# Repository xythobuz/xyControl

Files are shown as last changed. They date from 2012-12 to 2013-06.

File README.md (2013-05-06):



[xyControl][gh] is a Quadrocopter Flight Controller based on Atmels Atmega2560 microcontroller.
It features 512KB SRAM on-board, using the external memory interface of this processor.
Also included is a switched power supply as well as a USB connection to communicate with and program the target.
All I/O pins, including 3 additional UARTs, SPI, I2C (TWI) and 16 ADC Channels, are accessible via standard 2.54mm connectors.
The Board can be powered from an external stable 5V supply, USB or 7V or more, via the on-board switched power supply. All voltage sources can be selected via jumpers.

[][xy1]
[][xy2]
[][ss]

## Flight Control Software Flow

Three tasks are controlling the Quadrocopter Orientation in Space.

+ The [Orientation Task][orient] reads the Gyroscope and Accelerometer and calculates the current Roll and Pitch angles. They are stored in the global struct "orientation".
+ The [PID Task][pid] is then feeding these angles into two PID controllers. Their output is then used by...
+ The [Set Task][set], which calculates the motor speeds and gives them to...
+ The [motor task][motor], which sends the new values via TWI to the motor controllers.

# Supported Hardware

+ Gyroscope L3GD20, code based on the [Adafruit Example][adafruit].
+ Accelerometer and Magnetometer LSM303DLHC, code based on the [Pololu Example][pololucode].
+ I got both of these Sensors on the [MinIMU-9 v2][pololu].
+ Brushless Motor Driver [BL-Ctrl V1.2][ctrl] with eg. the [Robbe Roxxy Outrunner 2824-34][mot] Brushless Motor.
+ BTM-222 Bluetooth UART Bridge ([PCB][bt])

## External Memory ([xmem.h][xmem])

The external memory consists of a 512Kx8 SRAM, bank-switched onto the 16bit avr address space.
This gives us 8 memory banks, consisting of 56KB. All memory from 0x0000 to 0x21FF is the AVRs internal memory. The memory banks are switched into 0x2200 to 0xFFFF.
This gives us 8 banks with 56KB each, resulting in 448KB external RAM.

The data and bss memory sections, as well as the Stack are located in the internal RAM. The external RAM is used only for dynamically allocated memory.

## Orientation Calculation ([orientation.h][orient])

Calculates the current angles of the platform, using Gyroscope and Accelerometer Data with a Kalman Filter. It is using this slightly modified [Kalman Filter Implementation][kalman] by Linus Helgesson.

# PC and Android Tools

You can find some PC Software in the [tools][tools] directory. Each one should be accompanied by it's own Readme file.

## UART-Flight Status Packet Format

    printf("t%.2f %.2f %.2f\n", kp, ki, kd);
    printf("u%.2f %.2f\n", pid_output[1], pid_output[0]); // Pitch, Roll
    printf("v%i %i %i %i\n", motorSpeed[0], ..., motorSpeed[3]);
    printf("w%.2f\n", orientation.pitch);
    printf("x%.2f\n", orientation.roll);
    printf("y%.2f\n", orientation.yaw);
    printf("z%.2f\n", getVoltage());

# Software used

 + [Peter Fleurys TWI Library][fleury]

# License

Peter Fleurys TWI Library (twi.c & twi.h) is released under the [GNU GPL license][gpl].

Everything else is released under a BSD-Style license. See the [accompanying COPYING file][bsd].

 [sss]: http://www.xythobuz.de/img/xyCopterOsci_small.png
 [ss]: http://www.xythobuz.de/img/xyCopterOsci.png
 [xy1s]: http://www.xythobuz.de/img/xycontrol1_small.jpg
 [xy1]: http://www.xythobuz.de/img/xycontrol1.jpg
 [xy2s]: http://www.xythobuz.de/img/xycontrol2_small.jpg
 [xy2]: http://www.xythobuz.de/img/xycontrol2.jpg
 [gh]: http://www.xythobuz.de/xycontrol/
 [logo]: http://www.xythobuz.de/xycontrol/logo.png
 [adafruit]: https://github.com/adafruit/Adafruit_L3GD20
 [pololucode]: https://github.com/pololu/LSM303
 [pololu]: http://www.pololu.com/catalog/product/1268
 [ctrl]: http://www.mikrokopter.de/ucwiki/en/BL-Ctrl_V1.2
 [mot]: http://www.conrad.de/ce/de/product/231867
 [bt]: http://xythobuz.de/bluetooth.html
 [kalman]: http://www.linushelgesson.se/2012/04/pitch-and-roll-estimating-kalman-filter-for-stabilizing-quadrocopters/
 [fleury]: http://homepage.hispeed.ch/peterfleury/avr-software.html
 [gpl]: http://www.gnu.org/licenses/gpl.html
 [bsd]: https://github.com/xythobuz/xyControl/blob/master/COPYING
 [xmem]: https://github.com/xythobuz/xyControl/blob/master/include/xmem.h
 [orient]: https://github.com/xythobuz/xyControl/blob/master/include/orientation.h
 [tools]: https://github.com/xythobuz/xyControl/tree/master/tools
 [pid]: https://github.com/xythobuz/xyControl/blob/master/include/pid.h
 [set]: https://github.com/xythobuz/xyControl/blob/master/include/set.h
 [motor]: https://github.com/xythobuz/xyControl/blob/master/include/motor.h

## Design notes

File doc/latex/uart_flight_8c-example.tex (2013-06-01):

\hypertarget{uart_flight_8c-example}{\section{uart\-Flight.\-c}
}

\begin{DoxyCodeInclude}
\textcolor{comment}{/*}
\textcolor{comment}{ * uartFlight.c}
\textcolor{comment}{ *}
\textcolor{comment}{ * Copyright (c) 2013, Thomas Buck <xythobuz@me.com>}
\textcolor{comment}{ * All rights reserved.}
\textcolor{comment}{ *}
\textcolor{comment}{ * Redistribution and use in source and binary forms, with or without}
\textcolor{comment}{ * modification, are permitted provided that the following conditions}
\textcolor{comment}{ * are met:}
\textcolor{comment}{ *}
\textcolor{comment}{ * - Redistributions of source code must retain the above copyright notice,}
\textcolor{comment}{ *   this list of conditions and the following disclaimer.}
\textcolor{comment}{ *}
\textcolor{comment}{ * - Redistributions in binary form must reproduce the above copyright}
\textcolor{comment}{ *   notice, this list of conditions and the following disclaimer in the}
\textcolor{comment}{ *   documentation and/or other materials provided with the distribution.}
\textcolor{comment}{ *}
\textcolor{comment}{ * THIS SOFTWARE IS PROVIDED BY THE COPYRIGHT HOLDERS AND CONTRIBUTORS}
\textcolor{comment}{ * "AS IS" AND ANY EXPRESS OR IMPLIED WARRANTIES, INCLUDING, BUT NOT LIMITED}
\textcolor{comment}{ * TO, THE IMPLIED WARRANTIES OF MERCHANTABILITY AND FITNESS FOR A PARTICULAR}
\textcolor{comment}{ * PURPOSE ARE DISCLAIMED. IN NO EVENT SHALL THE COPYRIGHT HOLDER OR}
\textcolor{comment}{ * CONTRIBUTORS BE LIABLE FOR ANY DIRECT, INDIRECT, INCIDENTAL, SPECIAL,}
\textcolor{comment}{ * EXEMPLARY, OR CONSEQUENTIAL DAMAGES (INCLUDING, BUT NOT LIMITED TO,}
\textcolor{comment}{ * PROCUREMENT OF SUBSTITUTE GOODS OR SERVICES; LOSS OF USE, DATA, OR}
\textcolor{comment}{ * PROFITS; OR BUSINESS INTERRUPTION) HOWEVER CAUSED AND ON ANY THEORY OF}
\textcolor{comment}{ * LIABILITY, WHETHER IN CONTRACT, STRICT LIABILITY, OR TORT (INCLUDING}
\textcolor{comment}{ * NEGLIGENCE OR OTHERWISE) ARISING IN ANY WAY OUT OF THE USE OF THIS}
\textcolor{comment}{ * SOFTWARE, EVEN IF ADVISED OF THE POSSIBILITY OF SUCH DAMAGE.}
\textcolor{comment}{ */}
\textcolor{preprocessor}{#include <stdint.h>}
\textcolor{preprocessor}{#include <stdlib.h>}
\textcolor{preprocessor}{#include <stdio.h>}
\textcolor{preprocessor}{#include <avr/io.h>}
\textcolor{preprocessor}{#include <avr/pgmspace.h>}

\textcolor{preprocessor}{#define DEBUG 1}
\textcolor{preprocessor}{}
\textcolor{preprocessor}{#include <\hyperlink{debug_8h}{debug.h}>}
\textcolor{preprocessor}{#include <\hyperlink{tasks_8h}{tasks.h}>}
\textcolor{preprocessor}{#include <\hyperlink{error_8h}{error.h}>}
\textcolor{preprocessor}{#include <\hyperlink{xycontrol_8h}{xycontrol.h}>}
\textcolor{preprocessor}{#include <\hyperlink{time_8h}{time.h}>}
\textcolor{preprocessor}{#include <\hyperlink{uart_menu_8h}{uartMenu.h}>}
\textcolor{preprocessor}{#include <\hyperlink{serial_8h}{serial.h}>}
\textcolor{preprocessor}{#include <\hyperlink{acc_8h}{acc.h}>}
\textcolor{preprocessor}{#include <\hyperlink{gyro_8h}{gyro.h}>}
\textcolor{preprocessor}{#include <\hyperlink{mag_8h}{mag.h}>}
\textcolor{preprocessor}{#include <\hyperlink{motor_8h}{motor.h}>}
\textcolor{preprocessor}{#include <\hyperlink{orientation_8h}{orientation.h}>}
\textcolor{preprocessor}{#include <\hyperlink{pid_8h}{pid.h}>}
\textcolor{preprocessor}{#include <\hyperlink{set_8h}{set.h}>}

\textcolor{preprocessor}{#define MAXANGLE 45}
\textcolor{preprocessor}{}\textcolor{preprocessor}{#define ANGLESTEP 10}
\textcolor{preprocessor}{}\textcolor{preprocessor}{#define MAXMOTOR 255}
\textcolor{preprocessor}{}\textcolor{preprocessor}{#define MOTORSTEP 10}
\textcolor{preprocessor}{}\textcolor{preprocessor}{#define QUADFREQ 100}
\textcolor{preprocessor}{}\textcolor{preprocessor}{#define STATUSFREQ 10}
\textcolor{preprocessor}{}
\textcolor{preprocessor}{#define QUADDELAY (1000 / QUADFREQ)}
\textcolor{preprocessor}{}\textcolor{preprocessor}{#define STATUSDELAY (1000 / STATUSFREQ)}
\textcolor{preprocessor}{}
\textcolor{keywordtype}{void} flightTask(\textcolor{keywordtype}{void});
\textcolor{keywordtype}{void} statusTask(\textcolor{keywordtype}{void});
\textcolor{keywordtype}{void} controlToggle(\textcolor{keywordtype}{void});
\textcolor{keywordtype}{void} motorToggle(\textcolor{keywordtype}{void});
\textcolor{keywordtype}{void} motorUp(\textcolor{keywordtype}{void});
\textcolor{keywordtype}{void} motorDown(\textcolor{keywordtype}{void});
\textcolor{keywordtype}{void} motorForward(\textcolor{keywordtype}{void});
\textcolor{keywordtype}{void} motorBackward(\textcolor{keywordtype}{void});
\textcolor{keywordtype}{void} motorLeft(\textcolor{keywordtype}{void});
\textcolor{keywordtype}{void} motorRight(\textcolor{keywordtype}{void});
\textcolor{keywordtype}{void} parameterChange(\textcolor{keywordtype}{void});
\textcolor{keywordtype}{void} silent(\textcolor{keywordtype}{void});
\textcolor{keywordtype}{void} printRaw(\textcolor{keywordtype}{void});

\textcolor{keywordtype}{char} PROGMEM motorToggleString[] = \textcolor{stringliteral}{"Motor On/Off"};
\textcolor{keywordtype}{char} PROGMEM motorUpString[] = \textcolor{stringliteral}{"Up"};
\textcolor{keywordtype}{char} PROGMEM motorDownString[] = \textcolor{stringliteral}{"Down"};
\textcolor{keywordtype}{char} PROGMEM motorLeftString[] = \textcolor{stringliteral}{"Left"};
\textcolor{keywordtype}{char} PROGMEM motorRightString[] = \textcolor{stringliteral}{"Right"};
\textcolor{keywordtype}{char} PROGMEM motorForwardString[] = \textcolor{stringliteral}{"Forwards"};
\textcolor{keywordtype}{char} PROGMEM motorBackwardString[] = \textcolor{stringliteral}{"Backwards"};
\textcolor{keywordtype}{char} PROGMEM controlToggleString[] = \textcolor{stringliteral}{"Toggle PID"};
\textcolor{keywordtype}{char} PROGMEM parameterChangeString[] = \textcolor{stringliteral}{"Change PID Params"};
\textcolor{keywordtype}{char} PROGMEM zeroString[] = \textcolor{stringliteral}{"Angles to Zero"};
\textcolor{keywordtype}{char} PROGMEM silentString[] = \textcolor{stringliteral}{"Toggle Status Output"};
\textcolor{keywordtype}{char} PROGMEM sensorString[] = \textcolor{stringliteral}{"Raw Sensor Data"};

\textcolor{preprocessor}{#define STATE\_MOTOR (1 << 0) // 1 -> Motor On}
\textcolor{preprocessor}{}\textcolor{preprocessor}{#define STATE\_PID (1 << 1) // 1 -> PID enabled}
\textcolor{preprocessor}{}\textcolor{preprocessor}{#define STATE\_OUTPUT (1 << 2) // 1 -> No Status Output}
\textcolor{preprocessor}{}uint8\_t state = 0;

uint8\_t speed = 10;
int16\_t targetRoll = 0;
int16\_t targetPitch = 0;

uint32\_t sumFlightTask = 0, countFlightTask = 0;

\textcolor{keywordtype}{int} main(\textcolor{keywordtype}{void}) \{
    \hyperlink{group__xycontrol_ga2b3fb0734a2675e6dbdcb2c7665a708f}{xyInit}();
    \hyperlink{group__pid_ga54768e126d9accbdd7232d9fa5adfdfd}{pidInit}();
    \hyperlink{group__motor_gaa29e2982047be0f7afbb10c8d6f3f5c3}{motorInit}();
    \hyperlink{group__orientation_gaa5724492d0f54b41a8984cdde51d59df}{orientationInit}();

    \hyperlink{group__debug_gada1787bea8c10cd89775d6918f6fd324}{debugPrint}(\textcolor{stringliteral}{"Initialized Hardware"});

    \hyperlink{group__task_ga9a6ba4cb66e2fb7e3be42fb5b87fec6f}{addTask}(&flightTask);
    \hyperlink{group__task_ga9a6ba4cb66e2fb7e3be42fb5b87fec6f}{addTask}(&statusTask);

    \hyperlink{group__uartmenu_gaba6c962adeaaeca40be02fb1098312ed}{addMenuCommand}(\textcolor{charliteral}{'m'}, motorToggleString, &motorToggle);
    \hyperlink{group__uartmenu_gaba6c962adeaaeca40be02fb1098312ed}{addMenuCommand}(\textcolor{charliteral}{'w'}, motorForwardString, &motorForward);
    \hyperlink{group__uartmenu_gaba6c962adeaaeca40be02fb1098312ed}{addMenuCommand}(\textcolor{charliteral}{'a'}, motorLeftString, &motorLeft);
    \hyperlink{group__uartmenu_gaba6c962adeaaeca40be02fb1098312ed}{addMenuCommand}(\textcolor{charliteral}{'s'}, motorBackwardString, &motorBackward);
    \hyperlink{group__uartmenu_gaba6c962adeaaeca40be02fb1098312ed}{addMenuCommand}(\textcolor{charliteral}{'d'}, motorRightString, &motorRight);
    \hyperlink{group__uartmenu_gaba6c962adeaaeca40be02fb1098312ed}{addMenuCommand}(\textcolor{charliteral}{'x'}, motorUpString, &motorUp);
    \hyperlink{group__uartmenu_gaba6c962adeaaeca40be02fb1098312ed}{addMenuCommand}(\textcolor{charliteral}{'y'}, motorDownString, &motorDown);
    \hyperlink{group__uartmenu_gaba6c962adeaaeca40be02fb1098312ed}{addMenuCommand}(\textcolor{charliteral}{'p'}, controlToggleString, &controlToggle);
    \hyperlink{group__uartmenu_gaba6c962adeaaeca40be02fb1098312ed}{addMenuCommand}(\textcolor{charliteral}{'n'}, parameterChangeString, &parameterChange);
    \hyperlink{group__uartmenu_gaba6c962adeaaeca40be02fb1098312ed}{addMenuCommand}(\textcolor{charliteral}{'z'}, zeroString, &\hyperlink{group__orientation_ga0fab95dd407145abad293f7c91460eee}{zeroOrientation});
    \hyperlink{group__uartmenu_gaba6c962adeaaeca40be02fb1098312ed}{addMenuCommand}(\textcolor{charliteral}{'o'}, silentString, &silent);
    \hyperlink{group__uartmenu_gaba6c962adeaaeca40be02fb1098312ed}{addMenuCommand}(\textcolor{charliteral}{'r'}, sensorString, &printRaw);

    \hyperlink{group__xycontrol_ga783aead7f97dd462a9af56b7fc3b228f}{xyLed}(\hyperlink{group__xycontrol_ggaadcb6002d2b42fdfe01490f730ab00a6ad80f13022b6d309268fadc7b1da89cb9}{LED\_RED}, \hyperlink{group__xycontrol_gga51a69e0b98357e170e63bc843e2fd1c0afc0ca8cc6cbe215fd3f1ae6d40255b40}{LED\_OFF});
    \hyperlink{group__xycontrol_ga783aead7f97dd462a9af56b7fc3b228f}{xyLed}(\hyperlink{group__xycontrol_ggaadcb6002d2b42fdfe01490f730ab00a6a0ad916c7f80666dc88f6b5b22a72e742}{LED\_GREEN}, \hyperlink{group__xycontrol_gga51a69e0b98357e170e63bc843e2fd1c0add01b80eb93658fb4cf7eb9aceb89a1d}{LED\_ON});

    \hyperlink{group__debug_gada1787bea8c10cd89775d6918f6fd324}{debugPrint}(\textcolor{stringliteral}{"Starting Tasks"});

    \textcolor{keywordflow}{for}(;;) \{
        \hyperlink{group__task_gabf4510e1aba7b08f11d447c2b530d661}{tasks}();
    \}

    \textcolor{keywordflow}{return} 0;
\}

\textcolor{keywordtype}{void} flightTask(\textcolor{keywordtype}{void}) \{
    \textcolor{keyword}{static} \hyperlink{group__time_ga02ad034d26db2c14b7e295b0c50fc11d}{time\_t} last = 100; \textcolor{comment}{// Don't begin immediately}
    \textcolor{keywordflow}{if} ((\hyperlink{group__time_ga158463b7abdb2191a9a364bce1faac83}{getSystemTime}() - last) >= QUADDELAY) \{
        last = \hyperlink{group__time_ga158463b7abdb2191a9a364bce1faac83}{getSystemTime}();
        \hyperlink{group__error_ga2c3e4bb40f36b262a5214e2da2bca9c5}{Error} e = \hyperlink{group__orientation_ga966edaeb4790aecd79b3c49ede459e56}{orientationTask}();
        \hyperlink{group__error_ga72d32a02ede7ed11eee387aa4f4c05d5}{REPORTERROR}(e);
        \textcolor{keywordflow}{if} (state & STATE\_PID) \{
            \hyperlink{group__pid_ga2683c9ee5bad3c89577ddc1bf16a219c}{pidTask}();
        \} \textcolor{keywordflow}{else} \{
            \hyperlink{group__pid_ga5b70790e470e0c5812d24a8a098c01e0}{pidOutput}[0] = \hyperlink{group__pid_ga5b70790e470e0c5812d24a8a098c01e0}{pidOutput}[1] = 0;
        \}
        \hyperlink{group__set_ga37f245c493d725009017f62a78505e64}{setTask}();
        \hyperlink{group__motor_gab10642c396b1a6dc22edf2b45288d781}{motorTask}();

        uint32\_t diff = \hyperlink{group__time_ga158463b7abdb2191a9a364bce1faac83}{getSystemTime}() - last;
        \textcolor{keywordflow}{if} (++countFlightTask >= QUADFREQ) \{
            countFlightTask = 1;
            sumFlightTask = diff;
        \} \textcolor{keywordflow}{else} \{
            sumFlightTask += diff;
        \}
    \}
\}

\textcolor{keywordtype}{void} statusTask(\textcolor{keywordtype}{void}) \{
    \textcolor{keyword}{static} \hyperlink{group__time_ga02ad034d26db2c14b7e295b0c50fc11d}{time\_t} last = 100; \textcolor{comment}{// Don't begin immediately}
    \textcolor{keyword}{static} uint32\_t lastDuration = 0;
    \textcolor{keywordflow}{if} (((\hyperlink{group__time_ga158463b7abdb2191a9a364bce1faac83}{getSystemTime}() - last) >= STATUSDELAY) && (!(state & STATE\_OUTPUT))) \{
        last = \hyperlink{group__time_ga158463b7abdb2191a9a364bce1faac83}{getSystemTime}();
        printf(\textcolor{stringliteral}{"p%.2f %.2f %.2f\(\backslash\)n"}, \hyperlink{group__orientation_gacd4a2942520b68691db5aebde4e537a4}{orientation}.\hyperlink{struct_angles_acd2ab495f15d37525f00fa358444a7e8}{vPitch}, 
      \hyperlink{group__orientation_gacd4a2942520b68691db5aebde4e537a4}{orientation}.\hyperlink{struct_angles_ae5dfe118046f69d156389c62c33de4fc}{vRoll}, \hyperlink{group__orientation_gacd4a2942520b68691db5aebde4e537a4}{orientation}.\hyperlink{struct_angles_a87a17eab9b8d06fdb255aae737aedcbf}{vYaw});
        printf(\textcolor{stringliteral}{"q%li %li\(\backslash\)n"}, sumFlightTask / countFlightTask, lastDuration);
        printf(\textcolor{stringliteral}{"r%.2f %.2f\(\backslash\)n"}, \hyperlink{group__pid_ga9ce36f9a8e0e12e30b448e0161e3e5ec}{pidStates}[0].intMin, \hyperlink{group__pid_ga9ce36f9a8e0e12e30b448e0161e3e5ec}{pidStates}[0].intMax);
        printf(\textcolor{stringliteral}{"s%.2f %.2f\(\backslash\)n"}, \hyperlink{group__pid_ga9ce36f9a8e0e12e30b448e0161e3e5ec}{pidStates}[0].outMin, \hyperlink{group__pid_ga9ce36f9a8e0e12e30b448e0161e3e5ec}{pidStates}[0].outMax);
        printf(\textcolor{stringliteral}{"t%.3f %.3f %.3f\(\backslash\)n"}, \hyperlink{group__pid_ga9ce36f9a8e0e12e30b448e0161e3e5ec}{pidStates}[0].kp, \hyperlink{group__pid_ga9ce36f9a8e0e12e30b448e0161e3e5ec}{pidStates}[0].ki, 
      \hyperlink{group__pid_ga9ce36f9a8e0e12e30b448e0161e3e5ec}{pidStates}[0].kd);
        printf(\textcolor{stringliteral}{"u%.2f %.2f\(\backslash\)n"}, \hyperlink{group__pid_ga5b70790e470e0c5812d24a8a098c01e0}{pidOutput}[\hyperlink{group__pid_gacd633835a520a62245ec6cfeb6d00e97}{PITCH}], \hyperlink{group__pid_ga5b70790e470e0c5812d24a8a098c01e0}{pidOutput}[
      \hyperlink{group__pid_gaf902416f65138704a180dbae2dc9d8f2}{ROLL}]);
        printf(\textcolor{stringliteral}{"v%i %i %i %i\(\backslash\)n"}, \hyperlink{group__motor_ga0b3c12451554c9ee060319cbe2553d3a}{motorSpeed}[0], \hyperlink{group__motor_ga0b3c12451554c9ee060319cbe2553d3a}{motorSpeed}[1], 
      \hyperlink{group__motor_ga0b3c12451554c9ee060319cbe2553d3a}{motorSpeed}[2], \hyperlink{group__motor_ga0b3c12451554c9ee060319cbe2553d3a}{motorSpeed}[3]);
        printf(\textcolor{stringliteral}{"w%.2f\(\backslash\)n"}, \hyperlink{group__orientation_gacd4a2942520b68691db5aebde4e537a4}{orientation}.\hyperlink{struct_angles_a34c057a0378030db67bd6a129f37d938}{pitch});
        printf(\textcolor{stringliteral}{"x%.2f\(\backslash\)n"}, \hyperlink{group__orientation_gacd4a2942520b68691db5aebde4e537a4}{orientation}.\hyperlink{struct_angles_a1d3228afa3a1d6773954f40c1e519eb9}{roll});
        printf(\textcolor{stringliteral}{"y%.2f\(\backslash\)n"}, \hyperlink{group__orientation_gacd4a2942520b68691db5aebde4e537a4}{orientation}.\hyperlink{struct_angles_a21cd490f6191f66678f55b4c242a10cf}{yaw});
        printf(\textcolor{stringliteral}{"z%.2f\(\backslash\)n"}, \hyperlink{group__xycontrol_ga97874cf2a7f8e6964188b54fe85084a6}{getVoltage}());
        lastDuration = \hyperlink{group__time_ga158463b7abdb2191a9a364bce1faac83}{getSystemTime}() - last;
    \}
\}

\textcolor{keywordtype}{void} controlToggle(\textcolor{keywordtype}{void}) \{
    \textcolor{keywordflow}{if} (state & STATE\_PID) \{
        state &= ~STATE\_PID;
        printf(\textcolor{stringliteral}{"PID Off!\(\backslash\)n"});
    \} \textcolor{keywordflow}{else} \{
        state |= STATE\_PID;
        printf(\textcolor{stringliteral}{"PID On!\(\backslash\)n"});
    \}
\}

\textcolor{keywordtype}{void} motorToggle(\textcolor{keywordtype}{void}) \{
    \textcolor{keywordflow}{if} (state & STATE\_MOTOR) \{
        state &= ~STATE\_MOTOR;
        \hyperlink{group__set_gab2b0c78a81e045d7a8f28be307b8c61b}{baseSpeed} = 0;
        printf(\textcolor{stringliteral}{"Motor Off!\(\backslash\)n"});
    \} \textcolor{keywordflow}{else} \{
        state |= STATE\_MOTOR;
        \hyperlink{group__set_gab2b0c78a81e045d7a8f28be307b8c61b}{baseSpeed} = speed = 10;
        printf(\textcolor{stringliteral}{"Motor On!\(\backslash\)n"});
    \}
\}

\textcolor{keywordtype}{void} motorUp(\textcolor{keywordtype}{void}) \{
    \textcolor{keywordflow}{if} (speed <= (MAXMOTOR - MOTORSTEP)) \{
        \textcolor{keywordflow}{if} (state & STATE\_MOTOR) \{
            speed += MOTORSTEP;
            \hyperlink{group__set_gab2b0c78a81e045d7a8f28be307b8c61b}{baseSpeed} = speed;
            printf(\textcolor{stringliteral}{"Throttle up to %i\(\backslash\)n"}, speed);
        \}
    \}
\}

\textcolor{keywordtype}{void} motorDown(\textcolor{keywordtype}{void}) \{
    \textcolor{keywordflow}{if} (speed >= MOTORSTEP) \{
        \textcolor{keywordflow}{if} (state & STATE\_MOTOR) \{
            speed -= MOTORSTEP;
            \hyperlink{group__set_gab2b0c78a81e045d7a8f28be307b8c61b}{baseSpeed} = speed;
            printf(\textcolor{stringliteral}{"Throttle down to %i\(\backslash\)n"}, speed);
        \}
    \}
\}

\textcolor{keywordtype}{void} motorForward(\textcolor{keywordtype}{void}) \{
    \textcolor{keywordflow}{if} (targetPitch >= (-1 * (MAXANGLE - ANGLESTEP))) \{
        targetPitch -= ANGLESTEP;
        \hyperlink{group__pid_ga260bc1ef7a231f2252e6e69e1e459ba6}{pidTarget}[\hyperlink{group__pid_gacd633835a520a62245ec6cfeb6d00e97}{PITCH}] = targetPitch;
        printf(\textcolor{stringliteral}{"Pitch Forward %i\(\backslash\)n"}, targetPitch);
    \}
\}

\textcolor{keywordtype}{void} motorBackward(\textcolor{keywordtype}{void}) \{
    \textcolor{keywordflow}{if} (targetPitch <= (MAXANGLE - ANGLESTEP)) \{
        targetPitch += ANGLESTEP;
        \hyperlink{group__pid_ga260bc1ef7a231f2252e6e69e1e459ba6}{pidTarget}[\hyperlink{group__pid_gacd633835a520a62245ec6cfeb6d00e97}{PITCH}] = targetPitch;
        printf(\textcolor{stringliteral}{"Pitch Backwards %i\(\backslash\)n"}, targetPitch);
    \}
\}

\textcolor{keywordtype}{void} motorLeft(\textcolor{keywordtype}{void}) \{
    \textcolor{keywordflow}{if} (targetRoll <= (MAXANGLE - ANGLESTEP)) \{
        targetRoll += ANGLESTEP;
        \hyperlink{group__pid_ga260bc1ef7a231f2252e6e69e1e459ba6}{pidTarget}[\hyperlink{group__pid_gaf902416f65138704a180dbae2dc9d8f2}{ROLL}] = targetRoll;
        printf(\textcolor{stringliteral}{"Roll Left %i\(\backslash\)n"}, targetRoll);
    \}
\}

\textcolor{keywordtype}{void} motorRight(\textcolor{keywordtype}{void}) \{
    \textcolor{keywordflow}{if} (targetRoll >= (-1 * (MAXANGLE - ANGLESTEP))) \{
        targetRoll -= ANGLESTEP;
        \hyperlink{group__pid_ga260bc1ef7a231f2252e6e69e1e459ba6}{pidTarget}[\hyperlink{group__pid_gaf902416f65138704a180dbae2dc9d8f2}{ROLL}] = targetRoll;
        printf(\textcolor{stringliteral}{"Roll Right %i\(\backslash\)n"}, targetRoll);
    \}
\}

\textcolor{keywordtype}{void} parameterChange(\textcolor{keywordtype}{void}) \{
    \textcolor{keywordtype}{double} p, i, d, min, max, iMin, iMax;
    \textcolor{keywordtype}{int} c = scanf(\textcolor{stringliteral}{"%lf %lf %lf %lf %lf %lf %lf"}, &p, &i, &d, &min, &max, &iMin, &iMax);
    \textcolor{keywordflow}{if} (c == 7) \{
        \hyperlink{group__pid_ga1fc5e60f994041f4a534f18d1f307308}{pidSet}(&\hyperlink{group__pid_ga9ce36f9a8e0e12e30b448e0161e3e5ec}{pidStates}[0], p, i, d, min, max, iMin, iMax);
        \hyperlink{group__pid_ga1fc5e60f994041f4a534f18d1f307308}{pidSet}(&\hyperlink{group__pid_ga9ce36f9a8e0e12e30b448e0161e3e5ec}{pidStates}[1], p, i, d, min, max, iMin, iMax);
    \} \textcolor{keywordflow}{else} \{
        printf(\textcolor{stringliteral}{"Only got %i (%lf %lf %lf %lf %lf %lf %lf)!\(\backslash\)n"}, c, p, i, d, min, max, iMin, iMax);
    \}
\}

\textcolor{keywordtype}{void} silent(\textcolor{keywordtype}{void}) \{
    \textcolor{keywordflow}{if} (state & STATE\_OUTPUT) \{
        \textcolor{comment}{// Currently disabled, bit set}
        state &= ~STATE\_OUTPUT; \textcolor{comment}{// Unset Bit}
    \} \textcolor{keywordflow}{else} \{
        \textcolor{comment}{// Currently enabled}
        state |= STATE\_OUTPUT; \textcolor{comment}{// Set Bit}
    \}
\}

\textcolor{keywordtype}{void} printRaw(\textcolor{keywordtype}{void}) \{
    \hyperlink{struct_vector3f}{Vector3f} v;
    \hyperlink{group__acc_ga4dd55defcab17af4ecc29562a5a28ab3}{accRead}(&v);
    printf(\textcolor{stringliteral}{"Ax: %f Ay: %f Az: %f\(\backslash\)n"}, v.\hyperlink{struct_vector3f_af88b946fb90d5f08b5fb740c70e98c10}{x}, v.\hyperlink{struct_vector3f_ab927965981178aa1fba979a37168db2a}{y}, v.\hyperlink{struct_vector3f_ab3e6ed577a7c669c19de1f9c1b46c872}{z});
    \hyperlink{group__gyro_gab90a6ac7c268152edb186ee699462fd8}{gyroRead}(&v);
    printf(\textcolor{stringliteral}{"Gx: %f Gy: %f Gz: %f\(\backslash\)n"}, v.\hyperlink{struct_vector3f_af88b946fb90d5f08b5fb740c70e98c10}{x}, v.\hyperlink{struct_vector3f_ab927965981178aa1fba979a37168db2a}{y}, v.\hyperlink{struct_vector3f_ab3e6ed577a7c669c19de1f9c1b46c872}{z});
    \hyperlink{group__mag_gacc0c83a48498170ef36451db2c684abb}{magRead}(&v);
    printf(\textcolor{stringliteral}{"Mx: %f My: %f Mz: %f\(\backslash\)n"}, v.\hyperlink{struct_vector3f_af88b946fb90d5f08b5fb740c70e98c10}{x}, v.\hyperlink{struct_vector3f_ab927965981178aa1fba979a37168db2a}{y}, v.\hyperlink{struct_vector3f_ab3e6ed577a7c669c19de1f9c1b46c872}{z});
\}
\end{DoxyCodeInclude}

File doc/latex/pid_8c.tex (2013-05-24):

\hypertarget{pid_8c}{\section{lib/pid.c File Reference}
\label{pid_8c}\index{lib/pid.\-c@{lib/pid.\-c}}
}

P\-I\-D Library Implementation.  

{\ttfamily \#include $<$stdint.\-h$>$}\\*
{\ttfamily \#include $<$avr/io.\-h$>$}\\*
{\ttfamily \#include $<$twi.\-h$>$}\\*
{\ttfamily \#include $<$motor.\-h$>$}\\*
{\ttfamily \#include $<$tasks.\-h$>$}\\*
{\ttfamily \#include $<$time.\-h$>$}\\*
{\ttfamily \#include $<$pid.\-h$>$}\\*
{\ttfamily \#include $<$orientation.\-h$>$}\\*
{\ttfamily \#include $<$config.\-h$>$}\\*
\subsection*{Functions}
\begin{DoxyCompactItemize}
\item 
double \hyperlink{group__pid_gaa373eb9da73ef4da4195fd5114555772}{pid\-Execute} (double should, double is, \hyperlink{struct_p_i_d_state}{P\-I\-D\-State} $\ast$state)
\begin{DoxyCompactList}\small\item\em Execute a single P\-I\-D Control Step. \end{DoxyCompactList}\item 
void \hyperlink{group__pid_ga54768e126d9accbdd7232d9fa5adfdfd}{pid\-Init} (void)
\begin{DoxyCompactList}\small\item\em Initialize Roll and Pitch P\-I\-D. \end{DoxyCompactList}\item 
void \hyperlink{group__pid_ga1fc5e60f994041f4a534f18d1f307308}{pid\-Set} (\hyperlink{struct_p_i_d_state}{P\-I\-D\-State} $\ast$pid, double kp, double ki, double kd, double min, double max, double i\-Min, double i\-Max)
\begin{DoxyCompactList}\small\item\em Set the parameters of a P\-I\-D controller. \end{DoxyCompactList}\item 
void \hyperlink{group__pid_ga2683c9ee5bad3c89577ddc1bf16a219c}{pid\-Task} (void)
\begin{DoxyCompactList}\small\item\em Step the Roll and Pitch P\-I\-D Controllers. \end{DoxyCompactList}\end{DoxyCompactItemize}
\subsection*{Variables}
\begin{DoxyCompactItemize}
\item 
\hyperlink{struct_p_i_d_state}{P\-I\-D\-State} \hyperlink{group__pid_ga9ce36f9a8e0e12e30b448e0161e3e5ec}{pid\-States} \mbox{[}2\mbox{]}
\begin{DoxyCompactList}\small\item\em Roll and Pitch P\-I\-D States. \end{DoxyCompactList}\item 
double \hyperlink{group__pid_ga260bc1ef7a231f2252e6e69e1e459ba6}{pid\-Target} \mbox{[}2\mbox{]}
\begin{DoxyCompactList}\small\item\em Roll and Pitch target angles. \end{DoxyCompactList}\item 
double \hyperlink{group__pid_ga5b70790e470e0c5812d24a8a098c01e0}{pid\-Output} \mbox{[}2\mbox{]}
\begin{DoxyCompactList}\small\item\em Roll and Pitch P\-I\-D Output. \end{DoxyCompactList}\end{DoxyCompactItemize}

\subsection{Detailed Description}
P\-I\-D Library Implementation. 

Definition in file \hyperlink{pid_8c_source}{pid.\-c}.

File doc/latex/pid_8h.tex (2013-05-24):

\hypertarget{pid_8h}{\section{include/pid.h File Reference}
\label{pid_8h}\index{include/pid.\-h@{include/pid.\-h}}
}

P\-I\-D Library Header.  

\subsection*{Data Structures}
\begin{DoxyCompactItemize}
\item 
struct \hyperlink{struct_p_i_d_state}{P\-I\-D\-State}
\begin{DoxyCompactList}\small\item\em Data Structure for a single P\-I\-D Controller. \end{DoxyCompactList}\end{DoxyCompactItemize}
\subsection*{Macros}
\begin{DoxyCompactItemize}
\item 
\#define \hyperlink{group__pid_gaf902416f65138704a180dbae2dc9d8f2}{R\-O\-L\-L}~0
\begin{DoxyCompactList}\small\item\em Roll index for \hyperlink{group__pid_ga260bc1ef7a231f2252e6e69e1e459ba6}{pid\-Target}, \hyperlink{group__pid_ga5b70790e470e0c5812d24a8a098c01e0}{pid\-Output} and \hyperlink{group__pid_ga9ce36f9a8e0e12e30b448e0161e3e5ec}{pid\-States}. \end{DoxyCompactList}\item 
\#define \hyperlink{group__pid_gacd633835a520a62245ec6cfeb6d00e97}{P\-I\-T\-C\-H}~1
\begin{DoxyCompactList}\small\item\em Pitch index for \hyperlink{group__pid_ga260bc1ef7a231f2252e6e69e1e459ba6}{pid\-Target}, \hyperlink{group__pid_ga5b70790e470e0c5812d24a8a098c01e0}{pid\-Output} and \hyperlink{group__pid_ga9ce36f9a8e0e12e30b448e0161e3e5ec}{pid\-States}. \end{DoxyCompactList}\end{DoxyCompactItemize}
\subsection*{Functions}
\begin{DoxyCompactItemize}
\item 
void \hyperlink{group__pid_ga54768e126d9accbdd7232d9fa5adfdfd}{pid\-Init} (void)
\begin{DoxyCompactList}\small\item\em Initialize Roll and Pitch P\-I\-D. \end{DoxyCompactList}\item 
void \hyperlink{group__pid_ga2683c9ee5bad3c89577ddc1bf16a219c}{pid\-Task} (void)
\begin{DoxyCompactList}\small\item\em Step the Roll and Pitch P\-I\-D Controllers. \end{DoxyCompactList}\item 
void \hyperlink{group__pid_ga1fc5e60f994041f4a534f18d1f307308}{pid\-Set} (\hyperlink{struct_p_i_d_state}{P\-I\-D\-State} $\ast$pid, double kp, double ki, double kd, double min, double max, double i\-Min, double i\-Max)
\begin{DoxyCompactList}\small\item\em Set the parameters of a P\-I\-D controller. \end{DoxyCompactList}\item 
double \hyperlink{group__pid_gaa373eb9da73ef4da4195fd5114555772}{pid\-Execute} (double should, double is, \hyperlink{struct_p_i_d_state}{P\-I\-D\-State} $\ast$state)
\begin{DoxyCompactList}\small\item\em Execute a single P\-I\-D Control Step. \end{DoxyCompactList}\end{DoxyCompactItemize}
\subsection*{Variables}
\begin{DoxyCompactItemize}
\item 
double \hyperlink{group__pid_ga260bc1ef7a231f2252e6e69e1e459ba6}{pid\-Target} \mbox{[}2\mbox{]}
\begin{DoxyCompactList}\small\item\em Roll and Pitch target angles. \end{DoxyCompactList}\item 
double \hyperlink{group__pid_ga5b70790e470e0c5812d24a8a098c01e0}{pid\-Output} \mbox{[}2\mbox{]}
\begin{DoxyCompactList}\small\item\em Roll and Pitch P\-I\-D Output. \end{DoxyCompactList}\item 
\hyperlink{struct_p_i_d_state}{P\-I\-D\-State} \hyperlink{group__pid_ga9ce36f9a8e0e12e30b448e0161e3e5ec}{pid\-States} \mbox{[}2\mbox{]}
\begin{DoxyCompactList}\small\item\em Roll and Pitch P\-I\-D States. \end{DoxyCompactList}\end{DoxyCompactItemize}

\subsection{Detailed Description}
P\-I\-D Library Header. 

Definition in file \hyperlink{pid_8h_source}{pid.\-h}.

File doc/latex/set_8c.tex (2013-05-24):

\hypertarget{set_8c}{\section{lib/set.c File Reference}
\label{set_8c}\index{lib/set.\-c@{lib/set.\-c}}
}

Motor Mixer Library Implementation.  

{\ttfamily \#include $<$stdint.\-h$>$}\\*
{\ttfamily \#include $<$avr/io.\-h$>$}\\*
{\ttfamily \#include $<$twi.\-h$>$}\\*
{\ttfamily \#include $<$motor.\-h$>$}\\*
{\ttfamily \#include $<$tasks.\-h$>$}\\*
{\ttfamily \#include $<$time.\-h$>$}\\*
{\ttfamily \#include $<$pid.\-h$>$}\\*
{\ttfamily \#include $<$set.\-h$>$}\\*
{\ttfamily \#include $<$config.\-h$>$}\\*
\subsection*{Functions}
\begin{DoxyCompactItemize}
\item 
void \hyperlink{group__set_ga4173baf06c19647e0c60ef2e910bbc87}{set\-Motor\-Speeds} (uint8\-\_\-t axis, uint8\-\_\-t $\ast$vals)
\begin{DoxyCompactList}\small\item\em Set the Motor Speeds according to the S\-E\-T\-\_\-$\ast$ Motor Position Constants. \end{DoxyCompactList}\item 
void \hyperlink{group__set_ga37f245c493d725009017f62a78505e64}{set\-Task} (void)
\begin{DoxyCompactList}\small\item\em Read the P\-I\-D Output and Set the Motor Speeds. \end{DoxyCompactList}\end{DoxyCompactItemize}
\subsection*{Variables}
\begin{DoxyCompactItemize}
\item 
uint8\-\_\-t \hyperlink{group__set_gab2b0c78a81e045d7a8f28be307b8c61b}{base\-Speed} = 0
\begin{DoxyCompactList}\small\item\em Motor Base Speed. \end{DoxyCompactList}\end{DoxyCompactItemize}

\subsection{Detailed Description}
Motor Mixer Library Implementation. 

Definition in file \hyperlink{set_8c_source}{set.\-c}.

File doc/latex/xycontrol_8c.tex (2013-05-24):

\hypertarget{xycontrol_8c}{\section{lib/xycontrol.c File Reference}
\label{xycontrol_8c}\index{lib/xycontrol.\-c@{lib/xycontrol.\-c}}
}

xy\-Control A\-P\-I Implementation.  

{\ttfamily \#include $<$avr/io.\-h$>$}\\*
{\ttfamily \#include $<$stdint.\-h$>$}\\*
{\ttfamily \#include $<$stdlib.\-h$>$}\\*
{\ttfamily \#include $<$stdio.\-h$>$}\\*
{\ttfamily \#include $<$avr/interrupt.\-h$>$}\\*
{\ttfamily \#include $<$avr/pgmspace.\-h$>$}\\*
{\ttfamily \#include $<$avr/wdt.\-h$>$}\\*
{\ttfamily \#include $<$serial.\-h$>$}\\*
{\ttfamily \#include $<$spi.\-h$>$}\\*
{\ttfamily \#include $<$time.\-h$>$}\\*
{\ttfamily \#include $<$xmem.\-h$>$}\\*
{\ttfamily \#include $<$xycontrol.\-h$>$}\\*
{\ttfamily \#include $<$twi.\-h$>$}\\*
{\ttfamily \#include $<$adc.\-h$>$}\\*
{\ttfamily \#include $<$uart\-Menu.\-h$>$}\\*
{\ttfamily \#include $<$tasks.\-h$>$}\\*
{\ttfamily \#include $<$config.\-h$>$}\\*
\subsection*{Functions}
\begin{DoxyCompactItemize}
\item 
int \hyperlink{group__xycontrol_ga7e2be90354ccc3af05947764858bc0b1}{uartoutput} (char c, F\-I\-L\-E $\ast$f)
\begin{DoxyCompactList}\small\item\em Method used to write to stdout and stderr. \end{DoxyCompactList}\item 
int \hyperlink{group__xycontrol_ga3f158de66529c4606b8d8a380e5a5b07}{uartinput} (F\-I\-L\-E $\ast$f)
\begin{DoxyCompactList}\small\item\em Method used to read from stdin. \end{DoxyCompactList}\item 
void \hyperlink{group__xycontrol_ga2b3fb0734a2675e6dbdcb2c7665a708f}{xy\-Init} (void)
\begin{DoxyCompactList}\small\item\em Initialize the xy\-Control Hardware. \end{DoxyCompactList}\item 
void \hyperlink{group__xycontrol_ga8b94cac17e75735eec6f6fa42d21ab72}{xy\-Led\-Internal} (uint8\-\_\-t v, volatile uint8\-\_\-t $\ast$port, uint8\-\_\-t pin)
\begin{DoxyCompactList}\small\item\em Internal L\-E\-D Manipulation function. \end{DoxyCompactList}\item 
double \hyperlink{group__xycontrol_ga97874cf2a7f8e6964188b54fe85084a6}{get\-Voltage} (void)
\begin{DoxyCompactList}\small\item\em Calculate and return the Battery Voltage. \end{DoxyCompactList}\item 
void \hyperlink{group__xycontrol_ga26f242fc9cc1fb7dfdb78daae5579a63}{xy\-Self\-Reset} (void)
\begin{DoxyCompactList}\small\item\em Use the Watchdog to reset yourself after 15ms. \end{DoxyCompactList}\item 
int64\-\_\-t \hyperlink{group__xycontrol_gabcbffb9fdac0122e1d64b53119d03c63}{map} (int64\-\_\-t value, int64\-\_\-t old\-Min, int64\-\_\-t old\-Max, int64\-\_\-t new\-Min, int64\-\_\-t new\-Max)
\begin{DoxyCompactList}\small\item\em Map an Integer from one range to another range. \end{DoxyCompactList}\end{DoxyCompactItemize}
\subsection*{Variables}
\begin{DoxyCompactItemize}
\item 
char P\-R\-O\-G\-M\-E\-M \hyperlink{group__xycontrol_gab29cf1c6b0f1a36311899902ec9364ea}{help\-Text} \mbox{[}$\,$\mbox{]} = \char`\"{}Print this Help\char`\"{}
\begin{DoxyCompactList}\small\item\em U\-A\-R\-T Menu Help Text. \end{DoxyCompactList}\item 
char P\-R\-O\-G\-M\-E\-M \hyperlink{group__xycontrol_ga27915b4caf41f74542980a4ea0f1726a}{reset\-Text} \mbox{[}$\,$\mbox{]} = \char`\"{}Reset M\-C\-U\char`\"{}
\begin{DoxyCompactList}\small\item\em U\-A\-R\-T Menu Reset Text. \end{DoxyCompactList}\item 
F\-I\-L\-E \hyperlink{group__xycontrol_gaad0ab56da43b41bbfeeaa3d1eca70e9c}{in\-File}
\begin{DoxyCompactList}\small\item\em F\-I\-L\-E for stdin. \end{DoxyCompactList}\item 
F\-I\-L\-E \hyperlink{group__xycontrol_gaa9e0cac6f45e381f488c1dd9a8418ca2}{out\-File}
\begin{DoxyCompactList}\small\item\em F\-I\-L\-E for stdout and stderr. \end{DoxyCompactList}\end{DoxyCompactItemize}

\subsection{Detailed Description}
xy\-Control A\-P\-I Implementation. 

Definition in file \hyperlink{xycontrol_8c_source}{xycontrol.\-c}.

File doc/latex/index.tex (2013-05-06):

\href{http://www.xythobuz.de/xycontrol/}{\tt xy\-Control} is a Quadrocopter Flight Controller based on Atmels Atmega2560 microcontroller. It features 512\-K\-B S\-R\-A\-M on-\/board, using the external memory interface of this processor. Also included is a switched power supply as well as a U\-S\-B connection to communicate with and program the target. All I/\-O pins, including 3 additional U\-A\-R\-Ts, S\-P\-I, I2\-C (T\-W\-I) and 16 A\-D\-C Channels, are accessible via standard 2.\-54mm connectors. The Board can be powered from an external stable 5\-V supply, U\-S\-B or 7\-V or more, via the on-\/board switched power supply. All voltage sources can be selected via jumpers.

\href{http://www.xythobuz.de/img/xycontrol1.jpg}{\tt !\mbox{[}Photo 1\mbox{]}\mbox{[}xy1s\mbox{]}} \href{http://www.xythobuz.de/img/xycontrol2.jpg}{\tt !\mbox{[}Photo 2\mbox{]}\mbox{[}xy2s\mbox{]}} \href{http://www.xythobuz.de/img/xyCopterOsci.png}{\tt !\mbox{[}Screenshot\mbox{]}\mbox{[}sss\mbox{]}}

\subsection*{Flight Control Software Flow}

Three tasks are controlling the Quadrocopter Orientation in Space.

\begin{DoxyItemize}
\item The \href{https://github.com/xythobuz/xyControl/blob/master/include/orientation.h}{\tt Orientation Task} reads the Gyroscope and Accelerometer and calculates the current Roll and Pitch angles. They are stored in the global struct \char`\"{}orientation\char`\"{}.
\item The \href{https://github.com/xythobuz/xyControl/blob/master/include/pid.h}{\tt P\-I\-D Task} is then feeding these angles into two P\-I\-D controllers. Their output is then used by...
\item The \href{https://github.com/xythobuz/xyControl/blob/master/include/set.h}{\tt Set Task}, which calculates the motor speeds and gives them to...
\item The \href{https://github.com/xythobuz/xyControl/blob/master/include/motor.h}{\tt motor task}, which sends the new values via T\-W\-I to the motor controllers.
\end{DoxyItemize}

\section*{Supported Hardware}

\begin{DoxyItemize}
\item Gyroscope L3\-G\-D20, code based on the \href{https://github.com/adafruit/Adafruit_L3GD20}{\tt Adafruit Example}.
\item Accelerometer and Magnetometer L\-S\-M303\-D\-L\-H\-C, code based on the \href{https://github.com/pololu/LSM303}{\tt Pololu Example}.
\item I got both of these Sensors on the \href{http://www.pololu.com/catalog/product/1268}{\tt Min\-I\-M\-U-\/9 v2}.
\item Brushless Motor Driver \href{http://www.mikrokopter.de/ucwiki/en/BL-Ctrl_V1.2}{\tt B\-L-\/\-Ctrl V1.\-2} with eg. the \href{http://www.conrad.de/ce/de/product/231867}{\tt Robbe Roxxy Outrunner 2824-\/34} Brushless Motor.
\item B\-T\-M-\/222 Bluetooth U\-A\-R\-T Bridge (\href{http://xythobuz.de/bluetooth.html}{\tt P\-C\-B})
\end{DoxyItemize}

\subsection*{External Memory (\href{https://github.com/xythobuz/xyControl/blob/master/include/xmem.h}{\tt xmem.\-h})}

The external memory consists of a 512\-Kx8 S\-R\-A\-M, bank-\/switched onto the 16bit avr address space. This gives us 8 memory banks, consisting of 56\-K\-B. All memory from 0x0000 to 0x21\-F\-F is the A\-V\-Rs internal memory. The memory banks are switched into 0x2200 to 0x\-F\-F\-F\-F. This gives us 8 banks with 56\-K\-B each, resulting in 448\-K\-B external R\-A\-M.

The data and bss memory sections, as well as the Stack are located in the internal R\-A\-M. The external R\-A\-M is used only for dynamically allocated memory.

\subsection*{Orientation Calculation (\href{https://github.com/xythobuz/xyControl/blob/master/include/orientation.h}{\tt orientation.\-h})}

Calculates the current angles of the platform, using Gyroscope and Accelerometer Data with a \hyperlink{struct_kalman}{Kalman} Filter. It is using this slightly modified \href{http://www.linushelgesson.se/2012/04/pitch-and-roll-estimating-kalman-filter-for-stabilizing-quadrocopters/}{\tt Kalman Filter Implementation} by Linus Helgesson.

\section*{P\-C and Android Tools}

You can find some P\-C Software in the \href{https://github.com/xythobuz/xyControl/tree/master/tools}{\tt tools} directory. Each one should be accompanied by it's own Readme file.

\subsection*{U\-A\-R\-T-\/\-Flight Status Packet Format}

\begin{DoxyVerb}printf("t%.2f %.2f %.2f\n", kp, ki, kd);
printf("u%.2f %.2f\n", pid_output[1], pid_output[0]); // Pitch, Roll
printf("v%i %i %i %i\n", motorSpeed[0], ..., motorSpeed[3]);
printf("w%.2f\n", orientation.pitch);
printf("x%.2f\n", orientation.roll);
printf("y%.2f\n", orientation.yaw);
printf("z%.2f\n", getVoltage());
\end{DoxyVerb}

\section*{Software used}

\begin{DoxyItemize}
\item \href{http://homepage.hispeed.ch/peterfleury/avr-software.html}{\tt Peter Fleurys T\-W\-I Library}
\end{DoxyItemize}

\section*{License}

Peter Fleurys T\-W\-I Library (\hyperlink{twi_8c_source}{twi.\-c} \& \hyperlink{twi_8h}{twi.\-h}) is released under the \href{http://www.gnu.org/licenses/gpl.html}{\tt G\-N\-U G\-P\-L license}.

Everything else is released under a B\-S\-D-\/\-Style license. See the \href{https://github.com/xythobuz/xyControl/blob/master/COPYING}{\tt accompanying C\-O\-P\-Y\-I\-N\-G file}.

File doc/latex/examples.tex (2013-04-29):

\section{Examples}
Here is a list of all examples\-:\begin{DoxyCompactItemize}
\item 
\hyperlink{hardware_test_8c-example}{hardware\-Test.\-c}
\item 
\hyperlink{test_8c-example}{test.\-c}
\item 
\hyperlink{uart_flight_8c-example}{uart\-Flight.\-c}
\end{DoxyCompactItemize}

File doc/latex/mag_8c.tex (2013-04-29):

\hypertarget{mag_8c}{\section{lib/mag.c File Reference}
\label{mag_8c}\index{lib/mag.\-c@{lib/mag.\-c}}
}

L\-S\-M303\-D\-L\-H\-C Magnetometer A\-P\-I Implementation.  

{\ttfamily \#include $<$avr/io.\-h$>$}\\*
{\ttfamily \#include $<$stdint.\-h$>$}\\*
{\ttfamily \#include $<$stdlib.\-h$>$}\\*
{\ttfamily \#include $<$twi.\-h$>$}\\*
{\ttfamily \#include $<$mag.\-h$>$}\\*
{\ttfamily \#include $<$error.\-h$>$}\\*
{\ttfamily \#include $<$config.\-h$>$}\\*
\subsection*{Macros}
\begin{DoxyCompactItemize}
\item 
\#define \hyperlink{group__mag_ga42f59dd3e4a9cb4d8d4dd4a1019b6ab5}{M\-A\-G\-R\-E\-G\-\_\-\-C\-R\-B}~0x01
\begin{DoxyCompactList}\small\item\em Magnetometer Gain Register. \end{DoxyCompactList}\item 
\#define \hyperlink{group__mag_ga54eabf3b296f6550c9f6d9826020c623}{M\-A\-G\-R\-E\-G\-\_\-\-M\-R}~0x02
\begin{DoxyCompactList}\small\item\em Magnetometer Mode Register. \end{DoxyCompactList}\item 
\#define \hyperlink{group__mag_ga84e94fce89f9ba26ff3f33621c3a63bd}{M\-A\-G\-R\-E\-G\-\_\-\-X\-H}~0x03
\begin{DoxyCompactList}\small\item\em First Magnetometer Output Register. \end{DoxyCompactList}\end{DoxyCompactItemize}
\subsection*{Functions}
\begin{DoxyCompactItemize}
\item 
\hyperlink{group__error_ga2c3e4bb40f36b262a5214e2da2bca9c5}{Error} \hyperlink{group__mag_gafaf03e3013fe2046847afc2518f23eed}{mag\-Write\-Register} (uint8\-\_\-t reg, uint8\-\_\-t val)
\begin{DoxyCompactList}\small\item\em Write a Magnetometer Register. \end{DoxyCompactList}\item 
\hyperlink{group__error_ga2c3e4bb40f36b262a5214e2da2bca9c5}{Error} \hyperlink{group__mag_ga7e5d5e6448efb84e8805e2fbea9cb374}{mag\-Init} (\hyperlink{group__mag_ga3af649d913d146d6654db2354d88c18a}{Mag\-Range} r)
\begin{DoxyCompactList}\small\item\em Initialize the Magnetometer. \end{DoxyCompactList}\item 
\hyperlink{group__error_ga2c3e4bb40f36b262a5214e2da2bca9c5}{Error} \hyperlink{group__mag_gacc0c83a48498170ef36451db2c684abb}{mag\-Read} (\hyperlink{struct_vector3f}{Vector3f} $\ast$v)
\begin{DoxyCompactList}\small\item\em Read from the Magnetometer. \end{DoxyCompactList}\end{DoxyCompactItemize}
\subsection*{Variables}
\begin{DoxyCompactItemize}
\item 
\hyperlink{group__mag_ga3af649d913d146d6654db2354d88c18a}{Mag\-Range} \hyperlink{group__mag_gaae12e12b371d0bcebe05462384a519a2}{mag\-Range}
\begin{DoxyCompactList}\small\item\em Stored range to scale returned values. \end{DoxyCompactList}\end{DoxyCompactItemize}

\subsection{Detailed Description}
L\-S\-M303\-D\-L\-H\-C Magnetometer A\-P\-I Implementation. 

Definition in file \hyperlink{mag_8c_source}{mag.\-c}.

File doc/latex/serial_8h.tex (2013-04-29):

\hypertarget{serial_8h}{\section{include/serial.h File Reference}
\label{serial_8h}\index{include/serial.\-h@{include/serial.\-h}}
}

U\-A\-R\-T Library Header File.  

\subsection*{Macros}
\begin{DoxyCompactItemize}
\item 
\#define \hyperlink{group__uart_ga779bf099075a999d1074357fccbd466b}{U\-S\-B}~0
\begin{DoxyCompactList}\small\item\em First U\-A\-R\-T Name. \end{DoxyCompactList}\item 
\#define \hyperlink{group__uart_ga3f30897fa8435dc9811642367a328be8}{B\-L\-U\-E\-T\-O\-O\-T\-H}~1
\begin{DoxyCompactList}\small\item\em Second U\-A\-R\-T Name. \end{DoxyCompactList}\item 
\#define \hyperlink{group__uart_gafccfd7d1315f0763ac404c6104883341}{B\-A\-U\-D}(baud\-Rate, xtal\-Cpu)~((xtal\-Cpu)/((baud\-Rate)$\ast$16l)-\/1)
\begin{DoxyCompactList}\small\item\em Calculate Baudrate Register Value. \end{DoxyCompactList}\end{DoxyCompactItemize}
\subsection*{Functions}
\begin{DoxyCompactItemize}
\item 
uint8\-\_\-t \hyperlink{group__uart_ga1ea963b291215ad9c5e8a0610f116b90}{serial\-Available} (void)
\begin{DoxyCompactList}\small\item\em Get number of available U\-A\-R\-T modules. \end{DoxyCompactList}\item 
void \hyperlink{group__uart_ga73d4335cb201753c580c87954f493886}{serial\-Init} (uint8\-\_\-t uart, uint16\-\_\-t baud)
\begin{DoxyCompactList}\small\item\em Initialize the U\-A\-R\-T Hardware. \end{DoxyCompactList}\item 
void \hyperlink{group__uart_gaa16a5ecaf9e40660ded50737ff1d0a88}{serial\-Close} (uint8\-\_\-t uart)
\begin{DoxyCompactList}\small\item\em Stop the U\-A\-R\-T Hardware. \end{DoxyCompactList}\item 
void \hyperlink{group__uart_ga5d5de9e3ed5a0be11f707113cfff33f5}{set\-Flow} (uint8\-\_\-t uart, uint8\-\_\-t on)
\begin{DoxyCompactList}\small\item\em Manually change the flow control. \end{DoxyCompactList}\item 
uint8\-\_\-t \hyperlink{group__uart_ga266a54dcf3c4b85d92bf6b16bdcb5069}{serial\-Has\-Char} (uint8\-\_\-t uart)
\begin{DoxyCompactList}\small\item\em Check if a byte was received. \end{DoxyCompactList}\item 
uint8\-\_\-t \hyperlink{group__uart_gaa9d6e44600b215154c3f66193df151f6}{serial\-Get} (uint8\-\_\-t uart)
\begin{DoxyCompactList}\small\item\em Read a single byte. \end{DoxyCompactList}\item 
uint8\-\_\-t \hyperlink{group__uart_gaf7c4238a9a5e8fff64af1faf1689a5a4}{serial\-Get\-Blocking} (uint8\-\_\-t uart)
\begin{DoxyCompactList}\small\item\em Wait until a character is received. \end{DoxyCompactList}\item 
uint8\-\_\-t \hyperlink{group__uart_ga73d16b244172336e7306ea2e4cf90fa1}{serial\-Rx\-Buffer\-Full} (uint8\-\_\-t uart)
\begin{DoxyCompactList}\small\item\em Check if the receive buffer is full. \end{DoxyCompactList}\item 
uint8\-\_\-t \hyperlink{group__uart_ga742268372398b85935564fded999b198}{serial\-Rx\-Buffer\-Empty} (uint8\-\_\-t uart)
\begin{DoxyCompactList}\small\item\em Check if the receive buffer is empty. \end{DoxyCompactList}\item 
void \hyperlink{group__uart_ga388583adaa7db4fad121b6454668b347}{serial\-Write} (uint8\-\_\-t uart, uint8\-\_\-t data)
\begin{DoxyCompactList}\small\item\em Send a byte. \end{DoxyCompactList}\item 
void \hyperlink{group__uart_ga054d68834f9ca19f3b2cf9d714337de4}{serial\-Write\-String} (uint8\-\_\-t uart, const char $\ast$data)
\begin{DoxyCompactList}\small\item\em Send a string. \end{DoxyCompactList}\item 
uint8\-\_\-t \hyperlink{group__uart_ga8a6adfd3c350ceb55605d003a62a36a4}{serial\-Tx\-Buffer\-Full} (uint8\-\_\-t uart)
\begin{DoxyCompactList}\small\item\em Check if the transmit buffer is full. \end{DoxyCompactList}\item 
uint8\-\_\-t \hyperlink{group__uart_ga14c345ea0707111e988a80ef1da65e32}{serial\-Tx\-Buffer\-Empty} (uint8\-\_\-t uart)
\begin{DoxyCompactList}\small\item\em Check if the transmit buffer is empty. \end{DoxyCompactList}\end{DoxyCompactItemize}

\subsection{Detailed Description}
U\-A\-R\-T Library Header File. 

Definition in file \hyperlink{serial_8h_source}{serial.\-h}.

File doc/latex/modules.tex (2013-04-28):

\section{Modules}
Here is a list of all modules\-:\begin{DoxyCompactList}
\item \contentsline{section}{Software}{\pageref{group___software}}{}
\begin{DoxyCompactList}
\item \contentsline{section}{System}{\pageref{group___system}}{}
\begin{DoxyCompactList}
\item \contentsline{section}{Debug Output}{\pageref{group__debug}}{}
\item \contentsline{section}{Error Reporting}{\pageref{group__error}}{}
\item \contentsline{section}{Task Handler}{\pageref{group__task}}{}
\item \contentsline{section}{Time Keeping}{\pageref{group__time}}{}
\item \contentsline{section}{U\-A\-R\-T Menu}{\pageref{group__uartmenu}}{}
\item \contentsline{section}{External Memory Interface}{\pageref{group__xmem}}{}
\item \contentsline{section}{xy\-Control Hardware}{\pageref{group__xycontrol}}{}
\end{DoxyCompactList}
\item \contentsline{section}{Flight}{\pageref{group___flight}}{}
\begin{DoxyCompactList}
\item \contentsline{section}{Complementary-\/\-Filter}{\pageref{group__complementary}}{}
\item \contentsline{section}{Kalman-\/\-Filter}{\pageref{group__kalman}}{}
\item \contentsline{section}{Orientation Calculation}{\pageref{group__orientation}}{}
\item \contentsline{section}{P\-I\-D-\/\-Controller}{\pageref{group__pid}}{}
\item \contentsline{section}{Motor Speed Mixer}{\pageref{group__set}}{}
\end{DoxyCompactList}
\end{DoxyCompactList}
\item \contentsline{section}{Hardware}{\pageref{group___hardware}}{}
\begin{DoxyCompactList}
\item \contentsline{section}{Accelerometer Driver}{\pageref{group__acc}}{}
\item \contentsline{section}{A\-D\-C Driver}{\pageref{group__adc}}{}
\item \contentsline{section}{Gyroscope Driver}{\pageref{group__gyro}}{}
\item \contentsline{section}{Magnetometer Driver}{\pageref{group__mag}}{}
\item \contentsline{section}{Motor Controller Driver}{\pageref{group__motor}}{}
\item \contentsline{section}{U\-A\-R\-T Library}{\pageref{group__uart}}{}
\item \contentsline{section}{S\-P\-I Driver}{\pageref{group__spi}}{}
\item \contentsline{section}{I2\-C Driver}{\pageref{group__twi}}{}
\end{DoxyCompactList}
\item \contentsline{section}{Configuration}{\pageref{group__config}}{}
\end{DoxyCompactList}

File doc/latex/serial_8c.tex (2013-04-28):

\hypertarget{serial_8c}{\section{lib/serial.c File Reference}
\label{serial_8c}\index{lib/serial.\-c@{lib/serial.\-c}}
}

U\-A\-R\-T Library Implementation.  

{\ttfamily \#include $<$avr/io.\-h$>$}\\*
{\ttfamily \#include $<$avr/interrupt.\-h$>$}\\*
{\ttfamily \#include $<$stdint.\-h$>$}\\*
{\ttfamily \#include \char`\"{}serial.\-h\char`\"{}}\\*
{\ttfamily \#include \char`\"{}serial\-\_\-device.\-h\char`\"{}}\\*
{\ttfamily \#include \char`\"{}config.\-h\char`\"{}}\\*
\subsection*{Macros}
\begin{DoxyCompactItemize}
\item 
\#define \hyperlink{group__uart_ga739a2a1a0047c98ac1b18ecd25dac092}{R\-X\-\_\-\-B\-U\-F\-F\-E\-R\-\_\-\-S\-I\-Z\-E}~32
\begin{DoxyCompactList}\small\item\em If you define this, a '\textbackslash{}r' (C\-R) will be put in front of a '\textbackslash{}n' (L\-F) when sending a byte. \end{DoxyCompactList}\item 
\#define \hyperlink{group__uart_ga9ab33647617098646990fe263600b650}{T\-X\-\_\-\-B\-U\-F\-F\-E\-R\-\_\-\-S\-I\-Z\-E}~16
\begin{DoxyCompactList}\small\item\em T\-X Buffer Size in Bytes (Power of 2) \end{DoxyCompactList}\item 
\#define \hyperlink{group__uart_gaff1f07741fbe1f53f46098687f0a05e2}{F\-L\-O\-W\-C\-O\-N\-T\-R\-O\-L}
\begin{DoxyCompactList}\small\item\em Defining this enables incoming X\-O\-N X\-O\-F\-F (sends X\-O\-F\-F if rx buff is full) \end{DoxyCompactList}\item 
\#define \hyperlink{group__uart_gaa7907a070ef8e6d68d7d774b34eebe66}{F\-L\-O\-W\-M\-A\-R\-K}~5
\begin{DoxyCompactList}\small\item\em Space remaining to trigger xoff/xon. \end{DoxyCompactList}\item 
\#define \hyperlink{group__uart_gacdf721774c51e08c6609e6fa8cf82cc9}{X\-O\-N}~0x11
\begin{DoxyCompactList}\small\item\em X\-O\-N Value. \end{DoxyCompactList}\item 
\#define \hyperlink{group__uart_ga67fd78ae15d2b67c10d44d69a49ab1c5}{X\-O\-F\-F}~0x13
\begin{DoxyCompactList}\small\item\em X\-O\-F\-F Value. \end{DoxyCompactList}\end{DoxyCompactItemize}
\subsection*{Functions}
\begin{DoxyCompactItemize}
\item 
uint8\-\_\-t \hyperlink{group__uart_ga1ea963b291215ad9c5e8a0610f116b90}{serial\-Available} (void)
\begin{DoxyCompactList}\small\item\em Get number of available U\-A\-R\-T modules. \end{DoxyCompactList}\item 
void \hyperlink{group__uart_ga73d4335cb201753c580c87954f493886}{serial\-Init} (uint8\-\_\-t uart, uint16\-\_\-t baud)
\begin{DoxyCompactList}\small\item\em Initialize the U\-A\-R\-T Hardware. \end{DoxyCompactList}\item 
void \hyperlink{group__uart_gaa16a5ecaf9e40660ded50737ff1d0a88}{serial\-Close} (uint8\-\_\-t uart)
\begin{DoxyCompactList}\small\item\em Stop the U\-A\-R\-T Hardware. \end{DoxyCompactList}\item 
void \hyperlink{group__uart_ga5d5de9e3ed5a0be11f707113cfff33f5}{set\-Flow} (uint8\-\_\-t uart, uint8\-\_\-t on)
\begin{DoxyCompactList}\small\item\em Manually change the flow control. \end{DoxyCompactList}\item 
uint8\-\_\-t \hyperlink{group__uart_ga266a54dcf3c4b85d92bf6b16bdcb5069}{serial\-Has\-Char} (uint8\-\_\-t uart)
\begin{DoxyCompactList}\small\item\em Check if a byte was received. \end{DoxyCompactList}\item 
uint8\-\_\-t \hyperlink{group__uart_gaf7c4238a9a5e8fff64af1faf1689a5a4}{serial\-Get\-Blocking} (uint8\-\_\-t uart)
\begin{DoxyCompactList}\small\item\em Wait until a character is received. \end{DoxyCompactList}\item 
uint8\-\_\-t \hyperlink{group__uart_gaa9d6e44600b215154c3f66193df151f6}{serial\-Get} (uint8\-\_\-t uart)
\begin{DoxyCompactList}\small\item\em Read a single byte. \end{DoxyCompactList}\item 
uint8\-\_\-t \hyperlink{group__uart_ga73d16b244172336e7306ea2e4cf90fa1}{serial\-Rx\-Buffer\-Full} (uint8\-\_\-t uart)
\begin{DoxyCompactList}\small\item\em Check if the receive buffer is full. \end{DoxyCompactList}\item 
uint8\-\_\-t \hyperlink{group__uart_ga742268372398b85935564fded999b198}{serial\-Rx\-Buffer\-Empty} (uint8\-\_\-t uart)
\begin{DoxyCompactList}\small\item\em Check if the receive buffer is empty. \end{DoxyCompactList}\item 
void \hyperlink{group__uart_ga388583adaa7db4fad121b6454668b347}{serial\-Write} (uint8\-\_\-t uart, uint8\-\_\-t data)
\begin{DoxyCompactList}\small\item\em Send a byte. \end{DoxyCompactList}\item 
void \hyperlink{group__uart_ga054d68834f9ca19f3b2cf9d714337de4}{serial\-Write\-String} (uint8\-\_\-t uart, const char $\ast$data)
\begin{DoxyCompactList}\small\item\em Send a string. \end{DoxyCompactList}\item 
uint8\-\_\-t \hyperlink{group__uart_ga8a6adfd3c350ceb55605d003a62a36a4}{serial\-Tx\-Buffer\-Full} (uint8\-\_\-t uart)
\begin{DoxyCompactList}\small\item\em Check if the transmit buffer is full. \end{DoxyCompactList}\item 
uint8\-\_\-t \hyperlink{group__uart_ga14c345ea0707111e988a80ef1da65e32}{serial\-Tx\-Buffer\-Empty} (uint8\-\_\-t uart)
\begin{DoxyCompactList}\small\item\em Check if the transmit buffer is empty. \end{DoxyCompactList}\end{DoxyCompactItemize}

\subsection{Detailed Description}
U\-A\-R\-T Library Implementation. 

Definition in file \hyperlink{serial_8c_source}{serial.\-c}.

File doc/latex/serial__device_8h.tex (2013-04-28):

\hypertarget{serial__device_8h}{\section{include/serial\-\_\-device.h File Reference}
\label{serial__device_8h}\index{include/serial\-\_\-device.\-h@{include/serial\-\_\-device.\-h}}
}

U\-A\-R\-T Library device-\/specific configuration.  

\subsection{Detailed Description}
U\-A\-R\-T Library device-\/specific configuration. Contains Register and Bit Positions for different A\-V\-R devices. 

Definition in file \hyperlink{serial__device_8h_source}{serial\-\_\-device.\-h}.

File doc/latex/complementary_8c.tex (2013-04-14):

\hypertarget{complementary_8c}{\section{lib/complementary.c File Reference}
\label{complementary_8c}\index{lib/complementary.\-c@{lib/complementary.\-c}}
}

Complementary-\/\-Filter Implementation.  

{\ttfamily \#include $<$stdint.\-h$>$}\\*
{\ttfamily \#include $<$avr/io.\-h$>$}\\*
{\ttfamily \#include $<$time.\-h$>$}\\*
{\ttfamily \#include $<$complementary.\-h$>$}\\*
{\ttfamily \#include $<$config.\-h$>$}\\*
\subsection*{Functions}
\begin{DoxyCompactItemize}
\item 
void \hyperlink{group__complementary_ga0e47610c4ee9fab65271c599db6cc24b}{complementary\-Init} (\hyperlink{struct_complementary}{Complementary} $\ast$data)
\begin{DoxyCompactList}\small\item\em Initialize a Complementary-\/\-State. \end{DoxyCompactList}\item 
void \hyperlink{group__complementary_gaa0b82ecce955806245736b228e0702d2}{complementary\-Execute} (\hyperlink{struct_complementary}{Complementary} $\ast$data, double acc, double gyro)
\begin{DoxyCompactList}\small\item\em Step the \hyperlink{struct_complementary}{Complementary} Filter. \end{DoxyCompactList}\end{DoxyCompactItemize}

\subsection{Detailed Description}
Complementary-\/\-Filter Implementation. 

Definition in file \hyperlink{complementary_8c_source}{complementary.\-c}.

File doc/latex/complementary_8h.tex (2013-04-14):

\hypertarget{complementary_8h}{\section{include/complementary.h File Reference}
\label{complementary_8h}\index{include/complementary.\-h@{include/complementary.\-h}}
}

Complementary-\/\-Filter Header.  

{\ttfamily \#include $<$time.\-h$>$}\\*
\subsection*{Data Structures}
\begin{DoxyCompactItemize}
\item 
struct \hyperlink{struct_complementary}{Complementary}
\begin{DoxyCompactList}\small\item\em Cmplementary-\/\-Filter State data. \end{DoxyCompactList}\end{DoxyCompactItemize}
\subsection*{Functions}
\begin{DoxyCompactItemize}
\item 
void \hyperlink{group__complementary_gaa0b82ecce955806245736b228e0702d2}{complementary\-Execute} (\hyperlink{struct_complementary}{Complementary} $\ast$data, double acc, double gyro)
\begin{DoxyCompactList}\small\item\em Step the \hyperlink{struct_complementary}{Complementary} Filter. \end{DoxyCompactList}\item 
void \hyperlink{group__complementary_ga0e47610c4ee9fab65271c599db6cc24b}{complementary\-Init} (\hyperlink{struct_complementary}{Complementary} $\ast$data)
\begin{DoxyCompactList}\small\item\em Initialize a Complementary-\/\-State. \end{DoxyCompactList}\end{DoxyCompactItemize}

\subsection{Detailed Description}
Complementary-\/\-Filter Header. 

Definition in file \hyperlink{complementary_8h_source}{complementary.\-h}.

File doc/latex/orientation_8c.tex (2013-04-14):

\hypertarget{orientation_8c}{\section{lib/orientation.c File Reference}
\label{orientation_8c}\index{lib/orientation.\-c@{lib/orientation.\-c}}
}

Orientation A\-P\-I Implementation.  

{\ttfamily \#include $<$avr/io.\-h$>$}\\*
{\ttfamily \#include $<$stdint.\-h$>$}\\*
{\ttfamily \#include $<$math.\-h$>$}\\*
{\ttfamily \#include $<$xycontrol.\-h$>$}\\*
{\ttfamily \#include $<$error.\-h$>$}\\*
{\ttfamily \#include $<$gyro.\-h$>$}\\*
{\ttfamily \#include $<$acc.\-h$>$}\\*
{\ttfamily \#include $<$mag.\-h$>$}\\*
{\ttfamily \#include $<$tasks.\-h$>$}\\*
{\ttfamily \#include $<$time.\-h$>$}\\*
{\ttfamily \#include $<$orientation.\-h$>$}\\*
{\ttfamily \#include $<$kalman.\-h$>$}\\*
{\ttfamily \#include $<$complementary.\-h$>$}\\*
{\ttfamily \#include $<$config.\-h$>$}\\*
\subsection*{Macros}
\begin{DoxyCompactItemize}
\item 
\#define \hyperlink{group__orientation_ga1697ca2f6c35ed996d8653b5b029d283}{T\-O\-D\-E\-G}(x)~((x $\ast$ 180) / M\-\_\-\-P\-I)
\begin{DoxyCompactList}\small\item\em Convert Radians to Degrees. \end{DoxyCompactList}\end{DoxyCompactItemize}
\subsection*{Functions}
\begin{DoxyCompactItemize}
\item 
\hyperlink{group__error_ga2c3e4bb40f36b262a5214e2da2bca9c5}{Error} \hyperlink{group__orientation_gaa5724492d0f54b41a8984cdde51d59df}{orientation\-Init} (void)
\begin{DoxyCompactList}\small\item\em Initializes the Orientation A\-P\-I. \end{DoxyCompactList}\item 
\hyperlink{group__error_ga2c3e4bb40f36b262a5214e2da2bca9c5}{Error} \hyperlink{group__orientation_ga966edaeb4790aecd79b3c49ede459e56}{orientation\-Task} (void)
\begin{DoxyCompactList}\small\item\em Calculate the current orientation. \end{DoxyCompactList}\item 
void \hyperlink{group__orientation_ga0fab95dd407145abad293f7c91460eee}{zero\-Orientation} (void)
\begin{DoxyCompactList}\small\item\em Sets the current orientation to zero. \end{DoxyCompactList}\end{DoxyCompactItemize}
\subsection*{Variables}
\begin{DoxyCompactItemize}
\item 
\hyperlink{struct_angles}{Angles} \hyperlink{group__orientation_gacd4a2942520b68691db5aebde4e537a4}{orientation} = \{.pitch = 0, .roll = 0, .yaw = 0\}
\begin{DoxyCompactList}\small\item\em Current Aircraft orientation. \end{DoxyCompactList}\item 
\hyperlink{struct_angles}{Angles} \hyperlink{group__orientation_gab42c272957b0a5cdc11845ade183c2f9}{orientation\-Error} = \{.pitch = 0, .roll = 0, .yaw = 0\}
\begin{DoxyCompactList}\small\item\em Current Aircraft orientation offset. \end{DoxyCompactList}\item 
\hyperlink{struct_kalman}{Kalman} \hyperlink{group__orientation_gaee2ebdd37342c4cfa69ce7ee1440fd1d}{pitch\-Data}
\begin{DoxyCompactList}\small\item\em Kalman-\/\-State for Pitch Angle. \end{DoxyCompactList}\item 
\hyperlink{struct_kalman}{Kalman} \hyperlink{group__orientation_ga327c51463b7ca66c1ed8d0f400ffbfec}{roll\-Data}
\begin{DoxyCompactList}\small\item\em Kalman-\/\-State for Roll Angle. \end{DoxyCompactList}\end{DoxyCompactItemize}

\subsection{Detailed Description}
Orientation A\-P\-I Implementation. 

Definition in file \hyperlink{orientation_8c_source}{orientation.\-c}.

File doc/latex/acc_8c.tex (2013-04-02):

\hypertarget{acc_8c}{\section{lib/acc.c File Reference}
\label{acc_8c}\index{lib/acc.\-c@{lib/acc.\-c}}
}

L\-S\-M303\-D\-L\-H\-C Accelerometer A\-P\-I Implementation.  

{\ttfamily \#include $<$avr/io.\-h$>$}\\*
{\ttfamily \#include $<$stdint.\-h$>$}\\*
{\ttfamily \#include $<$stdlib.\-h$>$}\\*
{\ttfamily \#include $<$twi.\-h$>$}\\*
{\ttfamily \#include $<$acc.\-h$>$}\\*
{\ttfamily \#include $<$error.\-h$>$}\\*
{\ttfamily \#include $<$config.\-h$>$}\\*
\subsection*{Macros}
\begin{DoxyCompactItemize}
\item 
\#define \hyperlink{group__acc_gae81a43863d896c9afe65cc45bf8db9dc}{A\-C\-C\-R\-E\-G\-\_\-\-C\-T\-R\-L1}~0x20
\begin{DoxyCompactList}\small\item\em Accelerometer Control Register 1. \end{DoxyCompactList}\item 
\#define \hyperlink{group__acc_ga4369b46f297623a18b9d937623b7f783}{A\-C\-C\-R\-E\-G\-\_\-\-C\-T\-R\-L4}~0x23
\begin{DoxyCompactList}\small\item\em Accelerometer Control Register 4. \end{DoxyCompactList}\item 
\#define \hyperlink{group__acc_ga9d03f89f2f3ef006967f84157a21075b}{A\-C\-C\-R\-E\-G\-\_\-\-X\-L}~0x28
\begin{DoxyCompactList}\small\item\em First Accelerometer Output Register. \end{DoxyCompactList}\end{DoxyCompactItemize}
\subsection*{Functions}
\begin{DoxyCompactItemize}
\item 
\hyperlink{group__error_ga2c3e4bb40f36b262a5214e2da2bca9c5}{Error} \hyperlink{group__acc_ga277bcee14b8033f6da9790a8afe03348}{acc\-Write\-Register} (uint8\-\_\-t reg, uint8\-\_\-t val)
\begin{DoxyCompactList}\small\item\em Write an Accelerometer Register. \end{DoxyCompactList}\item 
\hyperlink{group__error_ga2c3e4bb40f36b262a5214e2da2bca9c5}{Error} \hyperlink{group__acc_ga7674eb1b940f183abe5e0b0913a87613}{acc\-Init} (\hyperlink{group__acc_ga3d56e56c162b045de727006a11880324}{Acc\-Range} r)
\begin{DoxyCompactList}\small\item\em Initialize the Accelerometer. \end{DoxyCompactList}\item 
\hyperlink{group__error_ga2c3e4bb40f36b262a5214e2da2bca9c5}{Error} \hyperlink{group__acc_ga4dd55defcab17af4ecc29562a5a28ab3}{acc\-Read} (\hyperlink{struct_vector3f}{Vector3f} $\ast$v)
\begin{DoxyCompactList}\small\item\em Read from the Accelerometer. \end{DoxyCompactList}\end{DoxyCompactItemize}
\subsection*{Variables}
\begin{DoxyCompactItemize}
\item 
\hyperlink{group__acc_ga3d56e56c162b045de727006a11880324}{Acc\-Range} \hyperlink{group__acc_ga450bb9262f697cdcab7185674b9fc6a3}{acc\-Range}
\begin{DoxyCompactList}\small\item\em Stored range to scale returned values. \end{DoxyCompactList}\end{DoxyCompactItemize}

\subsection{Detailed Description}
L\-S\-M303\-D\-L\-H\-C Accelerometer A\-P\-I Implementation. 

Definition in file \hyperlink{acc_8c_source}{acc.\-c}.

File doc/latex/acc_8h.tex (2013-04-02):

\hypertarget{acc_8h}{\section{include/acc.h File Reference}
\label{acc_8h}\index{include/acc.\-h@{include/acc.\-h}}
}

L\-S\-M303\-D\-L\-H\-C Accelerometer A\-P\-I Header.  

{\ttfamily \#include $<$error.\-h$>$}\\*
{\ttfamily \#include $<$xycontrol.\-h$>$}\\*
\subsection*{Enumerations}
\begin{DoxyCompactItemize}
\item 
enum \hyperlink{group__acc_ga3d56e56c162b045de727006a11880324}{Acc\-Range} \{ \hyperlink{group__acc_gga3d56e56c162b045de727006a11880324a4a2974e8d1854463238577802e1253f4}{r2\-G}, 
\hyperlink{group__acc_gga3d56e56c162b045de727006a11880324a9b1fcfa48172993a069412d5eecd6689}{r4\-G}, 
\hyperlink{group__acc_gga3d56e56c162b045de727006a11880324ac131fa2bab37bb0c8e152a91ce2b6bcf}{r8\-G}, 
\hyperlink{group__acc_gga3d56e56c162b045de727006a11880324af3fee93850514c5235659c573611f183}{r16\-G}
 \}
\begin{DoxyCompactList}\small\item\em Accelerometer Range options. \end{DoxyCompactList}\end{DoxyCompactItemize}
\subsection*{Functions}
\begin{DoxyCompactItemize}
\item 
\hyperlink{group__error_ga2c3e4bb40f36b262a5214e2da2bca9c5}{Error} \hyperlink{group__acc_ga7674eb1b940f183abe5e0b0913a87613}{acc\-Init} (\hyperlink{group__acc_ga3d56e56c162b045de727006a11880324}{Acc\-Range} r)
\begin{DoxyCompactList}\small\item\em Initialize the Accelerometer. \end{DoxyCompactList}\item 
\hyperlink{group__error_ga2c3e4bb40f36b262a5214e2da2bca9c5}{Error} \hyperlink{group__acc_ga4dd55defcab17af4ecc29562a5a28ab3}{acc\-Read} (\hyperlink{struct_vector3f}{Vector3f} $\ast$v)
\begin{DoxyCompactList}\small\item\em Read from the Accelerometer. \end{DoxyCompactList}\end{DoxyCompactItemize}

\subsection{Detailed Description}
L\-S\-M303\-D\-L\-H\-C Accelerometer A\-P\-I Header. 

Definition in file \hyperlink{acc_8h_source}{acc.\-h}.

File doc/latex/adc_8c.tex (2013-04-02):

\hypertarget{adc_8c}{\section{lib/adc.c File Reference}
\label{adc_8c}\index{lib/adc.\-c@{lib/adc.\-c}}
}

Analog-\/to-\/\-Digital Converter A\-P\-I Implementation.  

{\ttfamily \#include $<$avr/io.\-h$>$}\\*
{\ttfamily \#include $<$stdint.\-h$>$}\\*
{\ttfamily \#include $<$adc.\-h$>$}\\*
\subsection*{Functions}
\begin{DoxyCompactItemize}
\item 
void \hyperlink{group__adc_ga658c8b976878603187b79166345319e0}{adc\-Init} (\hyperlink{group__adc_ga7fc3dc0de11790b4393b4be70d79a02f}{A\-D\-C\-Ref} ref)
\begin{DoxyCompactList}\small\item\em Initialize the A\-D\-C Hardware. \end{DoxyCompactList}\item 
void \hyperlink{group__adc_ga709f0e604f22040ae61dc7710f0adee5}{adc\-Start} (uint8\-\_\-t channel)
\begin{DoxyCompactList}\small\item\em Start a conversion on a given channel. \end{DoxyCompactList}\item 
uint8\-\_\-t \hyperlink{group__adc_gaf80150a2f4a38efa40fe1c314b6995ef}{adc\-Ready} (void)
\begin{DoxyCompactList}\small\item\em Check if a result is ready. \end{DoxyCompactList}\item 
uint16\-\_\-t \hyperlink{group__adc_ga50d95c156a0eaea87bd65f5abfc1b5cb}{adc\-Get} (uint8\-\_\-t next)
\begin{DoxyCompactList}\small\item\em Get the conversion results. \end{DoxyCompactList}\item 
void \hyperlink{group__adc_ga60d979fb3eb0c7cc9da721671ad7f2bc}{adc\-Close} (void)
\begin{DoxyCompactList}\small\item\em Disable the A\-D\-C to save energy. \end{DoxyCompactList}\end{DoxyCompactItemize}

\subsection{Detailed Description}
Analog-\/to-\/\-Digital Converter A\-P\-I Implementation. 

Definition in file \hyperlink{adc_8c_source}{adc.\-c}.

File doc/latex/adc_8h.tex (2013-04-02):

\hypertarget{adc_8h}{\section{include/adc.h File Reference}
\label{adc_8h}\index{include/adc.\-h@{include/adc.\-h}}
}

Analog-\/to-\/\-Digital Converter A\-P\-I Header.  

\subsection*{Enumerations}
\begin{DoxyCompactItemize}
\item 
enum \hyperlink{group__adc_ga7fc3dc0de11790b4393b4be70d79a02f}{A\-D\-C\-Ref} \{ \hyperlink{group__adc_gga7fc3dc0de11790b4393b4be70d79a02fa6e9ea4c6059ebc1e09b29a64afe26bd4}{A\-R\-E\-F}, 
\hyperlink{group__adc_gga7fc3dc0de11790b4393b4be70d79a02faead1f65bef727ff7542b8139baceae9c}{A\-V\-C\-C}, 
\hyperlink{group__adc_gga7fc3dc0de11790b4393b4be70d79a02fa46f5d50796c7975a87eedbd152f34126}{A\-I\-N\-T1}, 
\hyperlink{group__adc_gga7fc3dc0de11790b4393b4be70d79a02fa265a976440d52609d53c5f8bfe2dae34}{A\-I\-N\-T2}
 \}
\begin{DoxyCompactList}\small\item\em A\-D\-C Reference Voltage options. \end{DoxyCompactList}\end{DoxyCompactItemize}
\subsection*{Functions}
\begin{DoxyCompactItemize}
\item 
void \hyperlink{group__adc_ga658c8b976878603187b79166345319e0}{adc\-Init} (\hyperlink{group__adc_ga7fc3dc0de11790b4393b4be70d79a02f}{A\-D\-C\-Ref} ref)
\begin{DoxyCompactList}\small\item\em Initialize the A\-D\-C Hardware. \end{DoxyCompactList}\item 
void \hyperlink{group__adc_ga709f0e604f22040ae61dc7710f0adee5}{adc\-Start} (uint8\-\_\-t channel)
\begin{DoxyCompactList}\small\item\em Start a conversion on a given channel. \end{DoxyCompactList}\item 
uint8\-\_\-t \hyperlink{group__adc_gaf80150a2f4a38efa40fe1c314b6995ef}{adc\-Ready} (void)
\begin{DoxyCompactList}\small\item\em Check if a result is ready. \end{DoxyCompactList}\item 
uint16\-\_\-t \hyperlink{group__adc_ga50d95c156a0eaea87bd65f5abfc1b5cb}{adc\-Get} (uint8\-\_\-t next)
\begin{DoxyCompactList}\small\item\em Get the conversion results. \end{DoxyCompactList}\item 
void \hyperlink{group__adc_ga60d979fb3eb0c7cc9da721671ad7f2bc}{adc\-Close} (void)
\begin{DoxyCompactList}\small\item\em Disable the A\-D\-C to save energy. \end{DoxyCompactList}\end{DoxyCompactItemize}

\subsection{Detailed Description}
Analog-\/to-\/\-Digital Converter A\-P\-I Header. 

Definition in file \hyperlink{adc_8h_source}{adc.\-h}.

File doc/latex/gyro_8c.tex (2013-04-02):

\hypertarget{gyro_8c}{\section{lib/gyro.c File Reference}
\label{gyro_8c}\index{lib/gyro.\-c@{lib/gyro.\-c}}
}

L3\-G\-D20 Gyroscope A\-P\-I Implementation.  

{\ttfamily \#include $<$stdlib.\-h$>$}\\*
{\ttfamily \#include $<$stdint.\-h$>$}\\*
{\ttfamily \#include $<$avr/io.\-h$>$}\\*
{\ttfamily \#include $<$twi.\-h$>$}\\*
{\ttfamily \#include $<$gyro.\-h$>$}\\*
{\ttfamily \#include $<$error.\-h$>$}\\*
{\ttfamily \#include $<$config.\-h$>$}\\*
\subsection*{Macros}
\begin{DoxyCompactItemize}
\item 
\#define \hyperlink{group__gyro_ga59d5eec860eab49733b4a814731e356c}{G\-Y\-R\-O\-R\-E\-G\-\_\-\-C\-T\-R\-L1}~0x20
\begin{DoxyCompactList}\small\item\em Gyroscope Control Register 1. \end{DoxyCompactList}\item 
\#define \hyperlink{group__gyro_gae9b6f4aab3818fdb4c99970918e0a705}{G\-Y\-R\-O\-R\-E\-G\-\_\-\-C\-T\-R\-L4}~0x23
\begin{DoxyCompactList}\small\item\em Gyroscope Control Register 4. \end{DoxyCompactList}\item 
\#define \hyperlink{group__gyro_ga8840a0f1e53e6999ddf435a61c0dc279}{G\-Y\-R\-O\-R\-E\-G\-\_\-\-O\-U\-T\-X\-L}~0x28
\begin{DoxyCompactList}\small\item\em First Gyroscope Output Register. \end{DoxyCompactList}\end{DoxyCompactItemize}
\subsection*{Functions}
\begin{DoxyCompactItemize}
\item 
\hyperlink{group__error_ga2c3e4bb40f36b262a5214e2da2bca9c5}{Error} \hyperlink{group__gyro_ga779a6d1a0641fc1ddc530366f582961b}{gyro\-Write\-Byte} (uint8\-\_\-t reg, uint8\-\_\-t val)
\begin{DoxyCompactList}\small\item\em Write a Gyroscope Register. \end{DoxyCompactList}\item 
\hyperlink{group__error_ga2c3e4bb40f36b262a5214e2da2bca9c5}{Error} \hyperlink{group__gyro_ga276b9ab6ac85c65b5a55356c00958be7}{gyro\-Init} (\hyperlink{group__gyro_ga12b0e0572fdceaa90874f9364c862ead}{Gyro\-Range} r)
\begin{DoxyCompactList}\small\item\em Initializes the Gyroscope. \end{DoxyCompactList}\item 
\hyperlink{group__error_ga2c3e4bb40f36b262a5214e2da2bca9c5}{Error} \hyperlink{group__gyro_gab90a6ac7c268152edb186ee699462fd8}{gyro\-Read} (\hyperlink{struct_vector3f}{Vector3f} $\ast$v)
\begin{DoxyCompactList}\small\item\em Get a set of gyroscope data. \end{DoxyCompactList}\end{DoxyCompactItemize}
\subsection*{Variables}
\begin{DoxyCompactItemize}
\item 
\hyperlink{group__gyro_ga12b0e0572fdceaa90874f9364c862ead}{Gyro\-Range} \hyperlink{group__gyro_gaa2ed27a7e4a0d8a5f492ef6059a04615}{gyro\-Range}
\begin{DoxyCompactList}\small\item\em Stored range to scale returned values. \end{DoxyCompactList}\end{DoxyCompactItemize}

\subsection{Detailed Description}
L3\-G\-D20 Gyroscope A\-P\-I Implementation. 

Definition in file \hyperlink{gyro_8c_source}{gyro.\-c}.

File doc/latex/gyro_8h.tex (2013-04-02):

\hypertarget{gyro_8h}{\section{include/gyro.h File Reference}
\label{gyro_8h}\index{include/gyro.\-h@{include/gyro.\-h}}
}

L3\-G\-D20 Gyroscope A\-P\-I Header.  

{\ttfamily \#include $<$error.\-h$>$}\\*
{\ttfamily \#include $<$xycontrol.\-h$>$}\\*
\subsection*{Enumerations}
\begin{DoxyCompactItemize}
\item 
enum \hyperlink{group__gyro_ga12b0e0572fdceaa90874f9364c862ead}{Gyro\-Range} \{ \hyperlink{group__gyro_gga12b0e0572fdceaa90874f9364c862eadad13cb337046598ead5e1fd8de0536efd}{r250\-D\-P\-S}, 
\hyperlink{group__gyro_gga12b0e0572fdceaa90874f9364c862eadad107e50e2c89475d879bbb777f658ab3}{r500\-D\-P\-S}, 
\hyperlink{group__gyro_gga12b0e0572fdceaa90874f9364c862eada738587d78e73a4947f7d00572e6a09b3}{r2000\-D\-P\-S}
 \}
\begin{DoxyCompactList}\small\item\em Gyroscope Range options. \end{DoxyCompactList}\end{DoxyCompactItemize}
\subsection*{Functions}
\begin{DoxyCompactItemize}
\item 
\hyperlink{group__error_ga2c3e4bb40f36b262a5214e2da2bca9c5}{Error} \hyperlink{group__gyro_ga276b9ab6ac85c65b5a55356c00958be7}{gyro\-Init} (\hyperlink{group__gyro_ga12b0e0572fdceaa90874f9364c862ead}{Gyro\-Range} r)
\begin{DoxyCompactList}\small\item\em Initializes the Gyroscope. \end{DoxyCompactList}\item 
\hyperlink{group__error_ga2c3e4bb40f36b262a5214e2da2bca9c5}{Error} \hyperlink{group__gyro_gab90a6ac7c268152edb186ee699462fd8}{gyro\-Read} (\hyperlink{struct_vector3f}{Vector3f} $\ast$v)
\begin{DoxyCompactList}\small\item\em Get a set of gyroscope data. \end{DoxyCompactList}\end{DoxyCompactItemize}

\subsection{Detailed Description}
L3\-G\-D20 Gyroscope A\-P\-I Header. 

Definition in file \hyperlink{gyro_8h_source}{gyro.\-h}.

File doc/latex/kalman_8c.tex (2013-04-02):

\hypertarget{kalman_8c}{\section{lib/kalman.c File Reference}
\label{kalman_8c}\index{lib/kalman.\-c@{lib/kalman.\-c}}
}

Kalman-\/\-Filter Implementation.  

{\ttfamily \#include $<$stdint.\-h$>$}\\*
{\ttfamily \#include $<$avr/io.\-h$>$}\\*
{\ttfamily \#include $<$kalman.\-h$>$}\\*
{\ttfamily \#include $<$config.\-h$>$}\\*
\subsection*{Functions}
\begin{DoxyCompactItemize}
\item 
void \hyperlink{group__kalman_ga89613fd996739650842bef0089c28cb9}{kalman\-Init} (\hyperlink{struct_kalman}{Kalman} $\ast$data)
\begin{DoxyCompactList}\small\item\em Initialize a Kalman-\/\-State. \end{DoxyCompactList}\item 
void \hyperlink{group__kalman_ga008ac0878fbd45cbf8403f52387a34d1}{kalman\-Innovate} (\hyperlink{struct_kalman}{Kalman} $\ast$data, double z1, double z2)
\begin{DoxyCompactList}\small\item\em Step the \hyperlink{struct_kalman}{Kalman} Filter. \end{DoxyCompactList}\end{DoxyCompactItemize}

\subsection{Detailed Description}
Kalman-\/\-Filter Implementation. 

Definition in file \hyperlink{kalman_8c_source}{kalman.\-c}.

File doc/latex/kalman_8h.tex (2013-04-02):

\hypertarget{kalman_8h}{\section{include/kalman.h File Reference}
\label{kalman_8h}\index{include/kalman.\-h@{include/kalman.\-h}}
}

Kalman-\/\-Filter Header.  

\subsection*{Data Structures}
\begin{DoxyCompactItemize}
\item 
struct \hyperlink{struct_kalman}{Kalman}
\begin{DoxyCompactList}\small\item\em Kalman-\/\-Filter State data. \end{DoxyCompactList}\end{DoxyCompactItemize}
\subsection*{Functions}
\begin{DoxyCompactItemize}
\item 
void \hyperlink{group__kalman_ga008ac0878fbd45cbf8403f52387a34d1}{kalman\-Innovate} (\hyperlink{struct_kalman}{Kalman} $\ast$data, double z1, double z2)
\begin{DoxyCompactList}\small\item\em Step the \hyperlink{struct_kalman}{Kalman} Filter. \end{DoxyCompactList}\item 
void \hyperlink{group__kalman_ga89613fd996739650842bef0089c28cb9}{kalman\-Init} (\hyperlink{struct_kalman}{Kalman} $\ast$data)
\begin{DoxyCompactList}\small\item\em Initialize a Kalman-\/\-State. \end{DoxyCompactList}\end{DoxyCompactItemize}

\subsection{Detailed Description}
Kalman-\/\-Filter Header. 

Definition in file \hyperlink{kalman_8h_source}{kalman.\-h}.

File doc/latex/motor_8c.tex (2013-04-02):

\hypertarget{motor_8c}{\section{lib/motor.c File Reference}
\label{motor_8c}\index{lib/motor.\-c@{lib/motor.\-c}}
}

B\-L-\/\-Ctrl V1.\-2 Controller A\-P\-I Implementation.  

{\ttfamily \#include $<$stdint.\-h$>$}\\*
{\ttfamily \#include $<$avr/io.\-h$>$}\\*
{\ttfamily \#include $<$twi.\-h$>$}\\*
{\ttfamily \#include $<$motor.\-h$>$}\\*
{\ttfamily \#include $<$tasks.\-h$>$}\\*
{\ttfamily \#include $<$time.\-h$>$}\\*
{\ttfamily \#include $<$config.\-h$>$}\\*
\subsection*{Functions}
\begin{DoxyCompactItemize}
\item 
void \hyperlink{group__motor_gab10642c396b1a6dc22edf2b45288d781}{motor\-Task} (void)
\begin{DoxyCompactList}\small\item\em Send the values stored in \hyperlink{group__motor_ga0b3c12451554c9ee060319cbe2553d3a}{motor\-Speed} to the Controllers. \end{DoxyCompactList}\item 
void \hyperlink{group__motor_gaa29e2982047be0f7afbb10c8d6f3f5c3}{motor\-Init} (void)
\begin{DoxyCompactList}\small\item\em Initializes the motor control library. \end{DoxyCompactList}\item 
void \hyperlink{group__motor_gafde1750cdf4354c295108eec552d899d}{motor\-Set} (uint8\-\_\-t id, uint8\-\_\-t speed)
\begin{DoxyCompactList}\small\item\em Set the speed of one or all motors. \end{DoxyCompactList}\end{DoxyCompactItemize}
\subsection*{Variables}
\begin{DoxyCompactItemize}
\item 
uint8\-\_\-t \hyperlink{group__motor_ga0b3c12451554c9ee060319cbe2553d3a}{motor\-Speed} \mbox{[}\hyperlink{group__config_ga1a2c496f8bb7dbb5f1dfef5c32624a6d}{M\-O\-T\-O\-R\-C\-O\-U\-N\-T}\mbox{]}
\begin{DoxyCompactList}\small\item\em Speed for the four motors. \end{DoxyCompactList}\end{DoxyCompactItemize}

\subsection{Detailed Description}
B\-L-\/\-Ctrl V1.\-2 Controller A\-P\-I Implementation. 

Definition in file \hyperlink{motor_8c_source}{motor.\-c}.

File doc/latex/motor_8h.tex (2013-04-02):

\hypertarget{motor_8h}{\section{include/motor.h File Reference}
\label{motor_8h}\index{include/motor.\-h@{include/motor.\-h}}
}

B\-L-\/\-Ctrl V1.\-2 Controller A\-P\-I Header.  

{\ttfamily \#include $<$config.\-h$>$}\\*
\subsection*{Functions}
\begin{DoxyCompactItemize}
\item 
void \hyperlink{group__motor_gaa29e2982047be0f7afbb10c8d6f3f5c3}{motor\-Init} (void)
\begin{DoxyCompactList}\small\item\em Initializes the motor control library. \end{DoxyCompactList}\item 
void \hyperlink{group__motor_gafde1750cdf4354c295108eec552d899d}{motor\-Set} (uint8\-\_\-t id, uint8\-\_\-t speed)
\begin{DoxyCompactList}\small\item\em Set the speed of one or all motors. \end{DoxyCompactList}\item 
void \hyperlink{group__motor_gab10642c396b1a6dc22edf2b45288d781}{motor\-Task} (void)
\begin{DoxyCompactList}\small\item\em Send the values stored in \hyperlink{group__motor_ga0b3c12451554c9ee060319cbe2553d3a}{motor\-Speed} to the Controllers. \end{DoxyCompactList}\end{DoxyCompactItemize}
\subsection*{Variables}
\begin{DoxyCompactItemize}
\item 
uint8\-\_\-t \hyperlink{group__motor_ga0b3c12451554c9ee060319cbe2553d3a}{motor\-Speed} \mbox{[}\hyperlink{group__config_ga1a2c496f8bb7dbb5f1dfef5c32624a6d}{M\-O\-T\-O\-R\-C\-O\-U\-N\-T}\mbox{]}
\begin{DoxyCompactList}\small\item\em Speed for the four motors. \end{DoxyCompactList}\end{DoxyCompactItemize}

\subsection{Detailed Description}
B\-L-\/\-Ctrl V1.\-2 Controller A\-P\-I Header. 

Definition in file \hyperlink{motor_8h_source}{motor.\-h}.

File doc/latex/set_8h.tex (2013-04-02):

\hypertarget{set_8h}{\section{include/set.h File Reference}
\label{set_8h}\index{include/set.\-h@{include/set.\-h}}
}

Motor Mixer Library Header.  

\subsection*{Functions}
\begin{DoxyCompactItemize}
\item 
void \hyperlink{group__set_ga37f245c493d725009017f62a78505e64}{set\-Task} (void)
\begin{DoxyCompactList}\small\item\em Read the P\-I\-D Output and Set the Motor Speeds. \end{DoxyCompactList}\end{DoxyCompactItemize}
\subsection*{Variables}
\begin{DoxyCompactItemize}
\item 
uint8\-\_\-t \hyperlink{group__set_gab2b0c78a81e045d7a8f28be307b8c61b}{base\-Speed}
\begin{DoxyCompactList}\small\item\em Motor Base Speed. \end{DoxyCompactList}\end{DoxyCompactItemize}

\subsection{Detailed Description}
Motor Mixer Library Header. 

Definition in file \hyperlink{set_8h_source}{set.\-h}.

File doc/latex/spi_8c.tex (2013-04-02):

\hypertarget{spi_8c}{\section{lib/spi.c File Reference}
\label{spi_8c}\index{lib/spi.\-c@{lib/spi.\-c}}
}

S\-P\-I A\-P\-I Implementation.  

{\ttfamily \#include $<$stdint.\-h$>$}\\*
{\ttfamily \#include $<$avr/io.\-h$>$}\\*
{\ttfamily \#include $<$spi.\-h$>$}\\*
{\ttfamily \#include $<$config.\-h$>$}\\*
\subsection*{Functions}
\begin{DoxyCompactItemize}
\item 
uint8\-\_\-t \hyperlink{group__spi_ga0ba99d77c04fac21eff9c6ee91b60d43}{spi\-Send\-Byte} (uint8\-\_\-t d)
\begin{DoxyCompactList}\small\item\em Send and Receive one byte. \end{DoxyCompactList}\end{DoxyCompactItemize}

\subsection{Detailed Description}
S\-P\-I A\-P\-I Implementation. 

Definition in file \hyperlink{spi_8c_source}{spi.\-c}.

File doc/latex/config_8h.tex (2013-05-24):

\hypertarget{config_8h}{\section{include/config.h File Reference}
\label{config_8h}\index{include/config.\-h@{include/config.\-h}}
}

Various default settings.  

\subsection*{Macros}
\begin{DoxyCompactItemize}
\item 
\#define \hyperlink{group__config_gaf45c761b3bd949068c77712e21259564}{O\-R\-I\-E\-N\-T\-A\-T\-I\-O\-N\-\_\-\-F\-I\-L\-T\-E\-R}~F\-I\-L\-T\-E\-R\-\_\-\-K\-A\-L\-M\-A\-N
\begin{DoxyCompactList}\small\item\em Filter Implementation to be used. \end{DoxyCompactList}\item 
\#define \hyperlink{group__config_ga61cd22949cc88bd899de6b20cb61e959}{C\-O\-M\-P\-L\-E\-M\-E\-N\-T\-A\-R\-Y\-\_\-\-T\-A\-U}~0.\-5
\begin{DoxyCompactList}\small\item\em Time Contant for Low and High Pass Filter in the \hyperlink{struct_complementary}{Complementary} Filter. \end{DoxyCompactList}\item 
\#define \hyperlink{group__config_gaba06e7be57726e74f267a1622e7d720e}{S\-O\-F\-T\-W\-A\-R\-E\-L\-O\-W\-P\-A\-S\-S}~1
\begin{DoxyCompactList}\small\item\em Software Low-\/\-Pass on Gyro and A\-C\-C. \end{DoxyCompactList}\item 
\#define \hyperlink{group__config_gaace41596724b03f3f2b2ee28b7e87272}{A\-C\-C\-F\-I\-L\-T\-E\-R\-F\-A\-C\-T\-O\-R}~\hyperlink{group__config_gaba06e7be57726e74f267a1622e7d720e}{S\-O\-F\-T\-W\-A\-R\-E\-L\-O\-W\-P\-A\-S\-S}
\begin{DoxyCompactList}\small\item\em Accelerometer Low Pass Factor. \end{DoxyCompactList}\item 
\#define \hyperlink{group__config_ga1b5d47810976ecbfd688513246db3ba9}{G\-Y\-R\-O\-F\-I\-L\-T\-E\-R\-F\-A\-C\-T\-O\-R}~\hyperlink{group__config_gaba06e7be57726e74f267a1622e7d720e}{S\-O\-F\-T\-W\-A\-R\-E\-L\-O\-W\-P\-A\-S\-S}
\begin{DoxyCompactList}\small\item\em Gyroscope Low Pass Factor. \end{DoxyCompactList}\item 
\#define \hyperlink{group__config_gaf36e4eab421932a006c7df7e84f11cf0}{P\-I\-D\-\_\-\-O\-U\-T\-M\-A\-X}~256
\begin{DoxyCompactList}\small\item\em Maximum P\-I\-D Output. \end{DoxyCompactList}\item 
\#define \hyperlink{group__config_ga684067981e82e4827607d0b0558812cb}{P\-I\-D\-\_\-\-O\-U\-T\-M\-I\-N}~-\/256
\begin{DoxyCompactList}\small\item\em Minimum P\-I\-D Output. \end{DoxyCompactList}\item 
\#define \hyperlink{group__config_ga50582411cbb3f8a20ffd3aa2254ddf71}{P\-I\-D\-\_\-\-I\-N\-T\-M\-A\-X}~\hyperlink{group__config_gaf36e4eab421932a006c7df7e84f11cf0}{P\-I\-D\-\_\-\-O\-U\-T\-M\-A\-X}
\begin{DoxyCompactList}\small\item\em Maximum P\-I\-D Integral Sum. \end{DoxyCompactList}\item 
\#define \hyperlink{group__config_ga9ee651f30455f25b5ca4c4bb9a0a6e49}{P\-I\-D\-\_\-\-I\-N\-T\-M\-I\-N}~\hyperlink{group__config_ga684067981e82e4827607d0b0558812cb}{P\-I\-D\-\_\-\-O\-U\-T\-M\-I\-N}
\begin{DoxyCompactList}\small\item\em Minimal P\-I\-D Integral Sum. \end{DoxyCompactList}\item 
\#define \hyperlink{group__config_ga943f07034774ef1261d62cd0d3d1fec9}{D\-T}~0.\-01f
\begin{DoxyCompactList}\small\item\em Time Constant. \end{DoxyCompactList}\item 
\#define \hyperlink{group__config_ga0f32727853a3ac3d848701803c3b8688}{Q1}~5.\-0f
\begin{DoxyCompactList}\small\item\em Q Matrix Diagonal Element 1. \end{DoxyCompactList}\item 
\#define \hyperlink{group__config_gaf5bca4c32f8c6886a3d8c526d2e3e9a7}{Q2}~100.\-0f
\begin{DoxyCompactList}\small\item\em Q Matrix Diagonal Element 2. \end{DoxyCompactList}\item 
\#define \hyperlink{group__config_ga1d7d3dfd2c4618949c484c5e8369f05a}{Q3}~0.\-01f
\begin{DoxyCompactList}\small\item\em Q Matrix Diagonal Element 3. \end{DoxyCompactList}\item 
\#define \hyperlink{group__config_ga918f64eb53db8e8dc694f36a87646476}{R1}~1000.\-0f
\begin{DoxyCompactList}\small\item\em R Matrix Diagonal Element 1. \end{DoxyCompactList}\item 
\#define \hyperlink{group__config_ga7a255a2815b9453060f51c6eb22cfed8}{R2}~1000.\-0f
\begin{DoxyCompactList}\small\item\em R Matrix Diagonal Element 2. \end{DoxyCompactList}\item 
\#define \hyperlink{group__config_ga460dbe0039d252579c5ce8beef7cc709}{S\-E\-T\-\_\-\-R\-O\-L\-L\-P\-L\-U\-S}~1
\begin{DoxyCompactList}\small\item\em Second Motor at the Right. \end{DoxyCompactList}\item 
\#define \hyperlink{group__config_ga9921670161925a1d7b946aeb65d5767a}{S\-E\-T\-\_\-\-R\-O\-L\-L\-M\-I\-N\-U\-S}~3
\begin{DoxyCompactList}\small\item\em Fourth Motor at the Left. \end{DoxyCompactList}\item 
\#define \hyperlink{group__config_gaf0a00d922db66d875ca53f6db34e7307}{S\-E\-T\-\_\-\-P\-I\-T\-C\-H\-P\-L\-U\-S}~0
\begin{DoxyCompactList}\small\item\em First Motor at the Top. \end{DoxyCompactList}\item 
\#define \hyperlink{group__config_ga8c969dbb07dc504226fc2c69484b9768}{S\-E\-T\-\_\-\-P\-I\-T\-C\-H\-M\-I\-N\-U\-S}~2
\begin{DoxyCompactList}\small\item\em Third Motor at the Bottom. \end{DoxyCompactList}\item 
\#define \hyperlink{group__config_gab3ea7c9a4399d8844727806c960880ad}{P\-I\-D\-\_\-\-P}~5.\-0
\begin{DoxyCompactList}\small\item\em Default P\-I\-D P Constant. \end{DoxyCompactList}\item 
\#define \hyperlink{group__config_ga2dfd5fcf8dd0bee1de9007fe8e161886}{P\-I\-D\-\_\-\-I}~0.\-03
\begin{DoxyCompactList}\small\item\em Default P\-I\-D I Constant. \end{DoxyCompactList}\item 
\#define \hyperlink{group__config_ga2a442b8579a5c5f9526e824165125497}{P\-I\-D\-\_\-\-D}~-\/13.\-0
\begin{DoxyCompactList}\small\item\em Default P\-I\-D D Constant. \end{DoxyCompactList}\item 
\#define \hyperlink{group__config_ga1a2c496f8bb7dbb5f1dfef5c32624a6d}{M\-O\-T\-O\-R\-C\-O\-U\-N\-T}~4
\begin{DoxyCompactList}\small\item\em Amount of motors. \end{DoxyCompactList}\item 
\#define \hyperlink{group__config_gac873c87f494ea2b22e7eb5fc74ad5a82}{B\-A\-T\-T\-\_\-\-M\-A\-X}~15
\begin{DoxyCompactList}\small\item\em Battery Voltage Reference (A\-D\-C 5\-V) \end{DoxyCompactList}\item 
\#define \hyperlink{group__config_ga9fd748b19523c96052a2964d73a7b0f5}{B\-A\-T\-T\-\_\-\-C\-H\-A\-N\-N\-E\-L}~0
\begin{DoxyCompactList}\small\item\em A\-D\-C Channel for Battery. \end{DoxyCompactList}\item 
\#define \hyperlink{group__config_ga27341a8e1cb1a6ace5a5cf3caea1c99f}{A\-C\-C\-\_\-\-A\-D\-D\-R\-E\-S\-S}~0x32
\begin{DoxyCompactList}\small\item\em Accelerometer Address (0011001r) \end{DoxyCompactList}\item 
\#define \hyperlink{group__config_ga8ed1f343e82440b4ef900e5fe42d74f0}{G\-Y\-R\-O\-\_\-\-A\-D\-D\-R\-E\-S\-S}~0x\-D6
\begin{DoxyCompactList}\small\item\em Gyroscope Address (110101xr, x = 1) \end{DoxyCompactList}\item 
\#define \hyperlink{group__config_gade4e63fac819c67040e374f08d2d7230}{M\-A\-G\-\_\-\-A\-D\-D\-R\-E\-S\-S}~0x3\-C
\begin{DoxyCompactList}\small\item\em Magnetometer Address. \end{DoxyCompactList}\item 
\#define \hyperlink{group__config_ga6e8ab18bbb1ef1b1e929c627f18224a3}{M\-O\-T\-O\-R\-\_\-\-B\-A\-S\-E\-A\-D\-D\-R\-E\-S\-S}~0x52
\begin{DoxyCompactList}\small\item\em Address of first motor controller. \end{DoxyCompactList}\item 
\#define \hyperlink{group__config_gac0f99671c3447a31e5d3755e1f11ee1f}{L\-E\-D0\-P\-O\-R\-T}~P\-O\-R\-T\-L
\begin{DoxyCompactList}\small\item\em First L\-E\-D Port. \end{DoxyCompactList}\item 
\#define \hyperlink{group__config_ga86208659221ec2a932cd722dfc18101f}{L\-E\-D0\-D\-D\-R}~D\-D\-R\-L
\begin{DoxyCompactList}\small\item\em First L\-E\-D Data Direction Register. \end{DoxyCompactList}\item 
\#define \hyperlink{group__config_gab0e1f692e2b1fa1cdbb24a9926b3489d}{L\-E\-D0\-P\-I\-N}~P\-L6
\begin{DoxyCompactList}\small\item\em First L\-E\-D Pin. \end{DoxyCompactList}\item 
\#define \hyperlink{group__config_ga3931891a757b08dbdfeaa8afd4dcb664}{L\-E\-D1\-P\-O\-R\-T}~P\-O\-R\-T\-L
\begin{DoxyCompactList}\small\item\em Second L\-E\-D Port. \end{DoxyCompactList}\item 
\#define \hyperlink{group__config_gab0f33b52cdb68e643eba6cf583fb625f}{L\-E\-D1\-D\-D\-R}~D\-D\-R\-L
\begin{DoxyCompactList}\small\item\em Second L\-E\-D Data Direction Register. \end{DoxyCompactList}\item 
\#define \hyperlink{group__config_ga04d7aaffbb7b5afaf49acf8a3a39e33a}{L\-E\-D1\-P\-I\-N}~P\-L7
\begin{DoxyCompactList}\small\item\em Second L\-E\-D Pin. \end{DoxyCompactList}\item 
\#define \hyperlink{group__config_ga4b6e8cddebfbc6f1f5132eb93b92d60f}{L\-E\-D2\-P\-O\-R\-T}~P\-O\-R\-T\-G
\begin{DoxyCompactList}\small\item\em Third L\-E\-D Port. \end{DoxyCompactList}\item 
\#define \hyperlink{group__config_ga7e635626ee31b094da0a668476132577}{L\-E\-D2\-D\-D\-R}~D\-D\-R\-G
\begin{DoxyCompactList}\small\item\em Third L\-E\-D Data Direction Register. \end{DoxyCompactList}\item 
\#define \hyperlink{group__config_ga50070e632cb68d11f627c5ab60f88683}{L\-E\-D2\-P\-I\-N}~P\-G5
\begin{DoxyCompactList}\small\item\em Third L\-E\-D Pin. \end{DoxyCompactList}\item 
\#define \hyperlink{group__config_ga63df95c1a0ce0e770964ca35e4032fb6}{L\-E\-D3\-P\-O\-R\-T}~P\-O\-R\-T\-E
\begin{DoxyCompactList}\small\item\em Fourth L\-E\-D Port. \end{DoxyCompactList}\item 
\#define \hyperlink{group__config_ga09535652dd0ca340b20840c848cb6093}{L\-E\-D3\-D\-D\-R}~D\-D\-R\-E
\begin{DoxyCompactList}\small\item\em Fourth L\-E\-D Data Direction Register. \end{DoxyCompactList}\item 
\#define \hyperlink{group__config_ga2663b8fc01c4753562adc572cf12a5ed}{L\-E\-D3\-P\-I\-N}~P\-E2
\begin{DoxyCompactList}\small\item\em Fourth L\-E\-D Pin. \end{DoxyCompactList}\item 
\#define \hyperlink{group__config_gabeec1986c81588dde8863b7936028fc9}{B\-A\-N\-K0\-P\-O\-R\-T}~P\-O\-R\-T\-G
\begin{DoxyCompactList}\small\item\em First Bank Selection Port. \end{DoxyCompactList}\item 
\#define \hyperlink{group__config_gafba0bbf9336cfc754622a5e9b3d12d80}{B\-A\-N\-K0\-D\-D\-R}~D\-D\-R\-G
\begin{DoxyCompactList}\small\item\em First Bank Selection Data Direction Register. \end{DoxyCompactList}\item 
\#define \hyperlink{group__config_gaa176e9b2752f764cd7e7d9fd49d46af8}{B\-A\-N\-K0\-P\-I\-N}~P\-G3
\begin{DoxyCompactList}\small\item\em First Bank Selection Pin. \end{DoxyCompactList}\item 
\#define \hyperlink{group__config_ga8b3ee7126196f6e939989eae097c3ac4}{B\-A\-N\-K1\-P\-O\-R\-T}~P\-O\-R\-T\-G
\begin{DoxyCompactList}\small\item\em Second Bank Selection Port. \end{DoxyCompactList}\item 
\#define \hyperlink{group__config_gada13cb9312072b48628763a6e1fd50d3}{B\-A\-N\-K1\-D\-D\-R}~D\-D\-R\-G
\begin{DoxyCompactList}\small\item\em Second Bank Selection Data Direction Register. \end{DoxyCompactList}\item 
\#define \hyperlink{group__config_gacfebedc2067e3c52e6ae1f627afcc1e1}{B\-A\-N\-K1\-P\-I\-N}~P\-G4
\begin{DoxyCompactList}\small\item\em Second Bank Selection Pin. \end{DoxyCompactList}\item 
\#define \hyperlink{group__config_gad35afb0251524c201c2d60f3d035af32}{B\-A\-N\-K2\-P\-O\-R\-T}~P\-O\-R\-T\-L
\begin{DoxyCompactList}\small\item\em Third Bank Selection Port. \end{DoxyCompactList}\item 
\#define \hyperlink{group__config_ga62f56230c5f5f7220c44ab1c93d677ab}{B\-A\-N\-K2\-D\-D\-R}~D\-D\-R\-L
\begin{DoxyCompactList}\small\item\em Third Bank Selection Data Direction Register. \end{DoxyCompactList}\item 
\#define \hyperlink{group__config_ga74c95f6ccdb5e482e97a5af53ed74229}{B\-A\-N\-K2\-P\-I\-N}~P\-L5
\begin{DoxyCompactList}\small\item\em Third Bank Selection Pin. \end{DoxyCompactList}\item 
\#define \hyperlink{group__config_gab652052c0495e4b720b52cdcf83f535d}{S\-P\-I\-S\-S}~P\-B0
\begin{DoxyCompactList}\small\item\em S\-P\-I Slave Select Pin. \end{DoxyCompactList}\item 
\#define \hyperlink{group__config_ga739a2a1a0047c98ac1b18ecd25dac092}{R\-X\-\_\-\-B\-U\-F\-F\-E\-R\-\_\-\-S\-I\-Z\-E}~64
\begin{DoxyCompactList}\small\item\em U\-A\-R\-T Receive Buffer Size. \end{DoxyCompactList}\item 
\#define \hyperlink{group__config_ga9ab33647617098646990fe263600b650}{T\-X\-\_\-\-B\-U\-F\-F\-E\-R\-\_\-\-S\-I\-Z\-E}~64
\begin{DoxyCompactList}\small\item\em U\-A\-R\-T Transmit Buffer Size. \end{DoxyCompactList}\end{DoxyCompactItemize}

\subsection{Detailed Description}
Various default settings. 

Definition in file \hyperlink{config_8h_source}{config.\-h}.

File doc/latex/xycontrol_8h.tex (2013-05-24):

\hypertarget{xycontrol_8h}{\section{include/xycontrol.h File Reference}
\label{xycontrol_8h}\index{include/xycontrol.\-h@{include/xycontrol.\-h}}
}

xy\-Control A\-P\-I Header.  

\subsection*{Data Structures}
\begin{DoxyCompactItemize}
\item 
struct \hyperlink{struct_vector3f}{Vector3f}
\begin{DoxyCompactList}\small\item\em The global 3-\/\-Dimensional Floating Point Vector. \end{DoxyCompactList}\end{DoxyCompactItemize}
\subsection*{Enumerations}
\begin{DoxyCompactItemize}
\item 
enum \hyperlink{group__xycontrol_gaadcb6002d2b42fdfe01490f730ab00a6}{L\-E\-D} \{ \\*
\hyperlink{group__xycontrol_ggaadcb6002d2b42fdfe01490f730ab00a6abd50485e17442a345888be61d2074c40}{L\-E\-D\-\_\-\-R\-E\-D0} = 0, 
\hyperlink{group__xycontrol_ggaadcb6002d2b42fdfe01490f730ab00a6af706e3dc22e0cbc5d3c38bb45ee35922}{L\-E\-D\-\_\-\-R\-E\-D1} = 1, 
\hyperlink{group__xycontrol_ggaadcb6002d2b42fdfe01490f730ab00a6a9360f305ce504b55ff68922bab599c38}{L\-E\-D\-\_\-\-G\-R\-E\-E\-N0} = 2, 
\hyperlink{group__xycontrol_ggaadcb6002d2b42fdfe01490f730ab00a6a213b05e94b12e0bcee53b6de3df294f8}{L\-E\-D\-\_\-\-G\-R\-E\-E\-N1} = 3, 
\\*
\hyperlink{group__xycontrol_ggaadcb6002d2b42fdfe01490f730ab00a6ae4fd580189cac85429ebfa5cb71cd772}{L\-E\-D\-\_\-\-A\-L\-L} = 4, 
\hyperlink{group__xycontrol_ggaadcb6002d2b42fdfe01490f730ab00a6a2a797d26a32fb3bdc0f975e6955e2873}{L\-E\-D\-\_\-\-B\-I\-T\-M\-A\-P} = 5, 
\hyperlink{group__xycontrol_ggaadcb6002d2b42fdfe01490f730ab00a6ad80f13022b6d309268fadc7b1da89cb9}{L\-E\-D\-\_\-\-R\-E\-D} = 6, 
\hyperlink{group__xycontrol_ggaadcb6002d2b42fdfe01490f730ab00a6a0ad916c7f80666dc88f6b5b22a72e742}{L\-E\-D\-\_\-\-G\-R\-E\-E\-N} = 7
 \}
\begin{DoxyCompactList}\small\item\em Methods of addressing the L\-E\-Ds. \end{DoxyCompactList}\item 
enum \hyperlink{group__xycontrol_ga51a69e0b98357e170e63bc843e2fd1c0}{L\-E\-D\-State} \{ \hyperlink{group__xycontrol_gga51a69e0b98357e170e63bc843e2fd1c0afc0ca8cc6cbe215fd3f1ae6d40255b40}{L\-E\-D\-\_\-\-O\-F\-F} = 0, 
\hyperlink{group__xycontrol_gga51a69e0b98357e170e63bc843e2fd1c0add01b80eb93658fb4cf7eb9aceb89a1d}{L\-E\-D\-\_\-\-O\-N} = 1, 
\hyperlink{group__xycontrol_gga51a69e0b98357e170e63bc843e2fd1c0a1b3bca014fbbfe339c8e216d175bae2e}{L\-E\-D\-\_\-\-T\-O\-G\-G\-L\-E} = 2
 \}
\begin{DoxyCompactList}\small\item\em Possible states of the L\-E\-Ds. \end{DoxyCompactList}\end{DoxyCompactItemize}
\subsection*{Functions}
\begin{DoxyCompactItemize}
\item 
void \hyperlink{group__xycontrol_ga2b3fb0734a2675e6dbdcb2c7665a708f}{xy\-Init} (void)
\begin{DoxyCompactList}\small\item\em Initialize the xy\-Control Hardware. \end{DoxyCompactList}\item 
void \hyperlink{group__xycontrol_ga783aead7f97dd462a9af56b7fc3b228f}{xy\-Led} (\hyperlink{group__xycontrol_gaadcb6002d2b42fdfe01490f730ab00a6}{L\-E\-D} l, \hyperlink{group__xycontrol_ga51a69e0b98357e170e63bc843e2fd1c0}{L\-E\-D\-State} v)
\begin{DoxyCompactList}\small\item\em Set the L\-E\-Ds. \end{DoxyCompactList}\item 
double \hyperlink{group__xycontrol_ga97874cf2a7f8e6964188b54fe85084a6}{get\-Voltage} (void)
\begin{DoxyCompactList}\small\item\em Calculate and return the Battery Voltage. \end{DoxyCompactList}\item 
void \hyperlink{group__xycontrol_ga26f242fc9cc1fb7dfdb78daae5579a63}{xy\-Self\-Reset} (void)
\begin{DoxyCompactList}\small\item\em Use the Watchdog to reset yourself after 15ms. \end{DoxyCompactList}\item 
int64\-\_\-t \hyperlink{group__xycontrol_gabcbffb9fdac0122e1d64b53119d03c63}{map} (int64\-\_\-t value, int64\-\_\-t old\-Min, int64\-\_\-t old\-Max, int64\-\_\-t new\-Min, int64\-\_\-t new\-Max)
\begin{DoxyCompactList}\small\item\em Map an Integer from one range to another range. \end{DoxyCompactList}\end{DoxyCompactItemize}

\subsection{Detailed Description}
xy\-Control A\-P\-I Header. 

Definition in file \hyperlink{xycontrol_8h_source}{xycontrol.\-h}.

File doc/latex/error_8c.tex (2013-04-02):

\hypertarget{error_8c}{\section{lib/error.c File Reference}
\label{error_8c}\index{lib/error.\-c@{lib/error.\-c}}
}

Global listing of different error conditions.  

{\ttfamily \#include $<$avr/io.\-h$>$}\\*
{\ttfamily \#include $<$stdint.\-h$>$}\\*
{\ttfamily \#include $<$stdlib.\-h$>$}\\*
{\ttfamily \#include $<$avr/pgmspace.\-h$>$}\\*
{\ttfamily \#include $<$error.\-h$>$}\\*
\subsection*{Functions}
\begin{DoxyCompactItemize}
\item 
char $\ast$ \hyperlink{group__error_ga6ad4aa1b927ea2ceb2c29b5693ddee53}{get\-Error\-String} (\hyperlink{group__error_ga2c3e4bb40f36b262a5214e2da2bca9c5}{Error} e)
\begin{DoxyCompactList}\small\item\em Returns a human-\/readable error description. \end{DoxyCompactList}\end{DoxyCompactItemize}
\subsection*{Variables}
\begin{DoxyCompactItemize}
\item 
char P\-R\-O\-G\-M\-E\-M \hyperlink{error_8c_a606e4c5df4b690d69b3f5b08419d1a1f}{error0} \mbox{[}$\,$\mbox{]} = \char`\"{}Success\char`\"{}
\begin{DoxyCompactList}\small\item\em String for S\-U\-C\-C\-E\-S\-S. \end{DoxyCompactList}\item 
char P\-R\-O\-G\-M\-E\-M \hyperlink{error_8c_a8c75e4b02dca7170df6874a9cdac5188}{error1} \mbox{[}$\,$\mbox{]} = \char`\"{}T\-W\-I doesn't answer\char`\"{}
\begin{DoxyCompactList}\small\item\em String for T\-W\-I\-\_\-\-N\-O\-\_\-\-A\-N\-S\-W\-E\-R. \end{DoxyCompactList}\item 
char P\-R\-O\-G\-M\-E\-M \hyperlink{error_8c_ac4156338c38414394192bc974e6822a2}{error2} \mbox{[}$\,$\mbox{]} = \char`\"{}T\-W\-I could not write\char`\"{}
\begin{DoxyCompactList}\small\item\em String for T\-W\-I\-\_\-\-W\-R\-I\-T\-E\-\_\-\-E\-R\-R\-O\-R. \end{DoxyCompactList}\item 
char P\-R\-O\-G\-M\-E\-M \hyperlink{error_8c_a376b3e9849d80aa569593c88726107e8}{error3} \mbox{[}$\,$\mbox{]} = \char`\"{}Not enough memory\char`\"{}
\begin{DoxyCompactList}\small\item\em String for M\-A\-L\-L\-O\-C\-\_\-\-F\-A\-I\-L. \end{DoxyCompactList}\item 
char P\-R\-O\-G\-M\-E\-M \hyperlink{error_8c_ac75921789501655408a831adf93568ae}{error4} \mbox{[}$\,$\mbox{]} = \char`\"{}General \hyperlink{group__error_ga2c3e4bb40f36b262a5214e2da2bca9c5}{Error}\char`\"{}
\begin{DoxyCompactList}\small\item\em String for E\-R\-R\-O\-R. \end{DoxyCompactList}\item 
char P\-R\-O\-G\-M\-E\-M \hyperlink{error_8c_ace3f3055ca8e01442967177a33049806}{error5} \mbox{[}$\,$\mbox{]} = \char`\"{}Argument \hyperlink{group__error_ga2c3e4bb40f36b262a5214e2da2bca9c5}{Error}\char`\"{}
\begin{DoxyCompactList}\small\item\em String for A\-R\-G\-U\-M\-E\-N\-T\-\_\-\-E\-R\-R\-O\-R. \end{DoxyCompactList}\item 
P\-G\-M\-\_\-\-P P\-R\-O\-G\-M\-E\-M \hyperlink{error_8c_a0bb6d2621c3b908d06e6b1343f5a3873}{error\-Table} \mbox{[}$\,$\mbox{]}
\begin{DoxyCompactList}\small\item\em Array of all error descriptions in Flash Memory. \end{DoxyCompactList}\end{DoxyCompactItemize}

\subsection{Detailed Description}
Global listing of different error conditions. Can be returned to signalise error or success. Also allows to print human-\/readable error descriptions. 

Definition in file \hyperlink{error_8c_source}{error.\-c}.

\subsection{Variable Documentation}
\hypertarget{error_8c_a606e4c5df4b690d69b3f5b08419d1a1f}{\index{error.\-c@{error.\-c}!error0@{error0}}
\index{error0@{error0}!error.c@{error.\-c}}
\subsubsection[{error0}]{\setlength{\rightskip}{0pt plus 5cm}char P\-R\-O\-G\-M\-E\-M error0\mbox{[}$\,$\mbox{]} = \char`\"{}Success\char`\"{}}}\label{error_8c_a606e4c5df4b690d69b3f5b08419d1a1f}

String for S\-U\-C\-C\-E\-S\-S. 

Definition at line 43 of file error.\-c.

\hypertarget{error_8c_a8c75e4b02dca7170df6874a9cdac5188}{\index{error.\-c@{error.\-c}!error1@{error1}}
\index{error1@{error1}!error.c@{error.\-c}}
\subsubsection[{error1}]{\setlength{\rightskip}{0pt plus 5cm}char P\-R\-O\-G\-M\-E\-M error1\mbox{[}$\,$\mbox{]} = \char`\"{}T\-W\-I doesn't answer\char`\"{}}}\label{error_8c_a8c75e4b02dca7170df6874a9cdac5188}

String for T\-W\-I\-\_\-\-N\-O\-\_\-\-A\-N\-S\-W\-E\-R. 

Definition at line 44 of file error.\-c.

\hypertarget{error_8c_ac4156338c38414394192bc974e6822a2}{\index{error.\-c@{error.\-c}!error2@{error2}}
\index{error2@{error2}!error.c@{error.\-c}}
\subsubsection[{error2}]{\setlength{\rightskip}{0pt plus 5cm}char P\-R\-O\-G\-M\-E\-M error2\mbox{[}$\,$\mbox{]} = \char`\"{}T\-W\-I could not write\char`\"{}}}\label{error_8c_ac4156338c38414394192bc974e6822a2}

String for T\-W\-I\-\_\-\-W\-R\-I\-T\-E\-\_\-\-E\-R\-R\-O\-R. 

Definition at line 45 of file error.\-c.

\hypertarget{error_8c_a376b3e9849d80aa569593c88726107e8}{\index{error.\-c@{error.\-c}!error3@{error3}}
\index{error3@{error3}!error.c@{error.\-c}}
\subsubsection[{error3}]{\setlength{\rightskip}{0pt plus 5cm}char P\-R\-O\-G\-M\-E\-M error3\mbox{[}$\,$\mbox{]} = \char`\"{}Not enough memory\char`\"{}}}\label{error_8c_a376b3e9849d80aa569593c88726107e8}

String for M\-A\-L\-L\-O\-C\-\_\-\-F\-A\-I\-L. 

Definition at line 46 of file error.\-c.

\hypertarget{error_8c_ac75921789501655408a831adf93568ae}{\index{error.\-c@{error.\-c}!error4@{error4}}
\index{error4@{error4}!error.c@{error.\-c}}
\subsubsection[{error4}]{\setlength{\rightskip}{0pt plus 5cm}char P\-R\-O\-G\-M\-E\-M error4\mbox{[}$\,$\mbox{]} = \char`\"{}General {\bf Error}\char`\"{}}}\label{error_8c_ac75921789501655408a831adf93568ae}

String for E\-R\-R\-O\-R. 

Definition at line 47 of file error.\-c.

\hypertarget{error_8c_ace3f3055ca8e01442967177a33049806}{\index{error.\-c@{error.\-c}!error5@{error5}}
\index{error5@{error5}!error.c@{error.\-c}}
\subsubsection[{error5}]{\setlength{\rightskip}{0pt plus 5cm}char P\-R\-O\-G\-M\-E\-M error5\mbox{[}$\,$\mbox{]} = \char`\"{}Argument {\bf Error}\char`\"{}}}\label{error_8c_ace3f3055ca8e01442967177a33049806}

String for A\-R\-G\-U\-M\-E\-N\-T\-\_\-\-E\-R\-R\-O\-R. 

Definition at line 48 of file error.\-c.

\hypertarget{error_8c_a0bb6d2621c3b908d06e6b1343f5a3873}{\index{error.\-c@{error.\-c}!error\-Table@{error\-Table}}
\index{error\-Table@{error\-Table}!error.c@{error.\-c}}
\subsubsection[{error\-Table}]{\setlength{\rightskip}{0pt plus 5cm}P\-G\-M\-\_\-\-P P\-R\-O\-G\-M\-E\-M error\-Table\mbox{[}$\,$\mbox{]}}}\label{error_8c_a0bb6d2621c3b908d06e6b1343f5a3873}
{\bfseries Initial value\-:}
\begin{DoxyCode}
= \{
    \hyperlink{error_8c_a606e4c5df4b690d69b3f5b08419d1a1f}{error0}, \hyperlink{error_8c_a8c75e4b02dca7170df6874a9cdac5188}{error1}, \hyperlink{error_8c_ac4156338c38414394192bc974e6822a2}{error2}, \hyperlink{error_8c_a376b3e9849d80aa569593c88726107e8}{error3}, \hyperlink{error_8c_ac75921789501655408a831adf93568ae}{error4}, \hyperlink{error_8c_ace3f3055ca8e01442967177a33049806}{error5}
\}
\end{DoxyCode}

Array of all error descriptions in Flash Memory. 

Definition at line 51 of file error.\-c.

Referenced by get\-Error\-String().

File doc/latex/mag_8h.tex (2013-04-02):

\hypertarget{mag_8h}{\section{include/mag.h File Reference}
\label{mag_8h}\index{include/mag.\-h@{include/mag.\-h}}
}

L\-S\-M303\-D\-L\-H\-C Magnetometer A\-P\-I Header.  

{\ttfamily \#include $<$error.\-h$>$}\\*
{\ttfamily \#include $<$xycontrol.\-h$>$}\\*
\subsection*{Enumerations}
\begin{DoxyCompactItemize}
\item 
enum \hyperlink{group__mag_ga3af649d913d146d6654db2354d88c18a}{Mag\-Range} \{ \\*
\hyperlink{group__mag_gga3af649d913d146d6654db2354d88c18aa18e06791b32b1772765ff7e54d3e24fd}{r1g3} = 1, 
\hyperlink{group__mag_gga3af649d913d146d6654db2354d88c18aa8cab223a26c8b984d14dd7214ec4f5f6}{r1g9} = 2, 
\hyperlink{group__mag_gga3af649d913d146d6654db2354d88c18aa19f90e5cf717669e72908f8d8a1c9f89}{r2g5} = 3, 
\hyperlink{group__mag_gga3af649d913d146d6654db2354d88c18aa402a6d56b75bc48c8521500dd8b38bd8}{r4g0} = 4, 
\\*
\hyperlink{group__mag_gga3af649d913d146d6654db2354d88c18aaa7401534bd82cade38cbb47c0ff4223e}{r4g7} = 5, 
\hyperlink{group__mag_gga3af649d913d146d6654db2354d88c18aa815faf18742b2b13ba477eed930851f4}{r5g6} = 6, 
\hyperlink{group__mag_gga3af649d913d146d6654db2354d88c18aa1cb5526ddb90c9b33beb87c0d5ad97ee}{r8g1} = 7
 \}
\begin{DoxyCompactList}\small\item\em Magnetometer Range options. \end{DoxyCompactList}\end{DoxyCompactItemize}
\subsection*{Functions}
\begin{DoxyCompactItemize}
\item 
\hyperlink{group__error_ga2c3e4bb40f36b262a5214e2da2bca9c5}{Error} \hyperlink{group__mag_ga7e5d5e6448efb84e8805e2fbea9cb374}{mag\-Init} (\hyperlink{group__mag_ga3af649d913d146d6654db2354d88c18a}{Mag\-Range} r)
\begin{DoxyCompactList}\small\item\em Initialize the Magnetometer. \end{DoxyCompactList}\item 
\hyperlink{group__error_ga2c3e4bb40f36b262a5214e2da2bca9c5}{Error} \hyperlink{group__mag_gacc0c83a48498170ef36451db2c684abb}{mag\-Read} (\hyperlink{struct_vector3f}{Vector3f} $\ast$v)
\begin{DoxyCompactList}\small\item\em Read from the Magnetometer. \end{DoxyCompactList}\end{DoxyCompactItemize}

\subsection{Detailed Description}
L\-S\-M303\-D\-L\-H\-C Magnetometer A\-P\-I Header. 

Definition in file \hyperlink{mag_8h_source}{mag.\-h}.

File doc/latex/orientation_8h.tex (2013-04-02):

\hypertarget{orientation_8h}{\section{include/orientation.h File Reference}
\label{orientation_8h}\index{include/orientation.\-h@{include/orientation.\-h}}
}

Orientation A\-P\-I Header.  

{\ttfamily \#include $<$error.\-h$>$}\\*
\subsection*{Data Structures}
\begin{DoxyCompactItemize}
\item 
struct \hyperlink{struct_angles}{Angles}
\begin{DoxyCompactList}\small\item\em Can store orientation in Euler Space. \end{DoxyCompactList}\end{DoxyCompactItemize}
\subsection*{Functions}
\begin{DoxyCompactItemize}
\item 
\hyperlink{group__error_ga2c3e4bb40f36b262a5214e2da2bca9c5}{Error} \hyperlink{group__orientation_gaa5724492d0f54b41a8984cdde51d59df}{orientation\-Init} (void)
\begin{DoxyCompactList}\small\item\em Initializes the Orientation A\-P\-I. \end{DoxyCompactList}\item
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

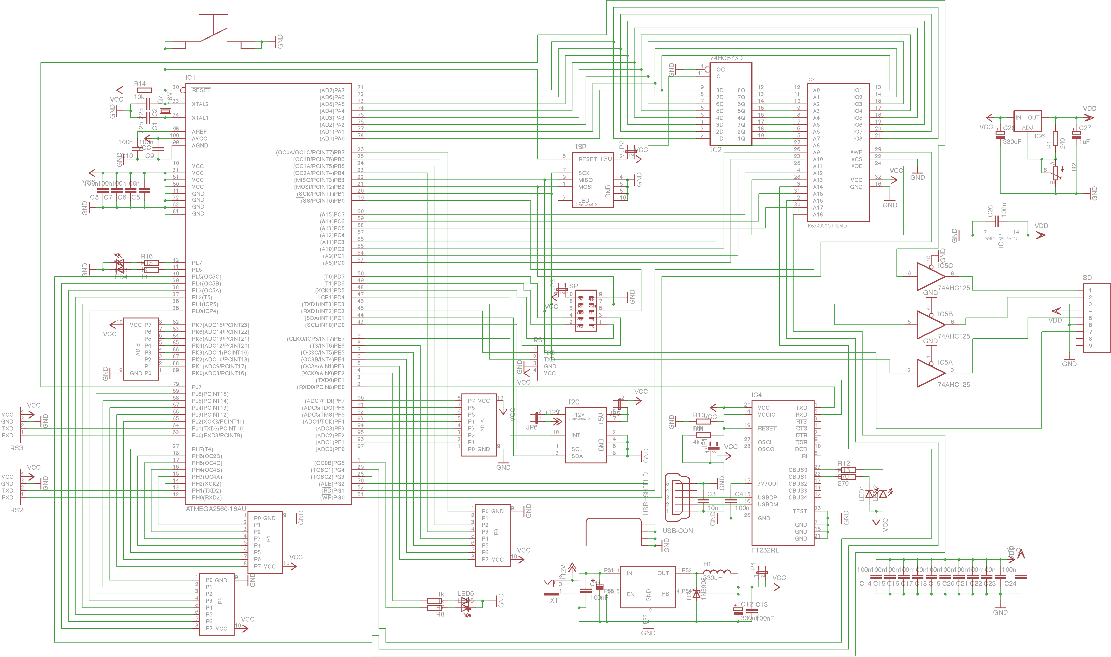
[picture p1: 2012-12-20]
Hardware/xyControl.png

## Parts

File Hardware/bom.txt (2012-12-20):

Partlist

C1 + C2     22p             0603
C3          10n             0603
C4 - C11    100n            0603
C12         330u            Elko SMD
C13 - C24   100n            0603
C25         100u            Elko SMD 6.5
C26         100n            0603
C27         1u              Elko 2.5 - 6
C28         330u            Elko 5 - 10.5

LED1        -               0603
LED2        -               0603
LED3        -               0603
LED4        -               0603
LED5        -               0603
LED6        -               0603

R1          240             0603
R2          2k5             Pot ST10
R7          1k              0603
R8          1k              0603
R10         10k             0603
R11         4k7             0603
R12         270             0603
R13         270             0603
R14         10k             0603
R15         1k              0603
R16         1k              0603

IC1         ATMEGA2560      TQFP100
IC2         74HC573D        SO20W
IC3         K6X4008C1FSMD   SOP-32
IC4         FT232RL         SSOP28
IC5         74AHC125        SO14
IC6         LM317L          TO-92
IC7         LM2576          TO-220

D2          1N5908          C4111-15
H1          330uH           PISR
Q7          16M             HC49/S

JP1         -               Jumper 1x2
JP2         -               Jumper 1x2
JP3         -               Jumper 1x2
JP4         -               Jumper 1x2
JP5         -               Jumper 1x2
JP6         -               Jumper 1x2
RS1         -               Jumper 1x4
RS2         -               Jumper 1x4
RS3         -               Jumper 1x4

SPI         -               ML10
I2C         -               ML10
AD-A        -               ML10
AD-B        -               ML10
P1          -               ML10
P2          -               ML10
P3          -               ML10
ISP         -               ML10

T1          -               SMD Button

USB         USB-B Mini      SMD
SD          -               FPS009-30003

X1          -               Conrad 733980-62

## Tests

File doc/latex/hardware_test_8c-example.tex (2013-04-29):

\hypertarget{hardware_test_8c-example}{\section{hardware\-Test.\-c}
}
Small walk-\/through the inner workings of the task scheduler and other library features.

\begin{DoxyCodeInclude}
\textcolor{comment}{/*}
\textcolor{comment}{ * hardwareTest.c}
\textcolor{comment}{ *}
\textcolor{comment}{ * Copyright (c) 2013, Thomas Buck <xythobuz@me.com>}
\textcolor{comment}{ * All rights reserved.}
\textcolor{comment}{ *}
\textcolor{comment}{ * Redistribution and use in source and binary forms, with or without}
\textcolor{comment}{ * modification, are permitted provided that the following conditions}
\textcolor{comment}{ * are met:}
\textcolor{comment}{ *}
\textcolor{comment}{ * - Redistributions of source code must retain the above copyright notice,}
\textcolor{comment}{ *   this list of conditions and the following disclaimer.}
\textcolor{comment}{ *}
\textcolor{comment}{ * - Redistributions in binary form must reproduce the above copyright}
\textcolor{comment}{ *   notice, this list of conditions and the following disclaimer in the}
\textcolor{comment}{ *   documentation and/or other materials provided with the distribution.}
\textcolor{comment}{ *}
\textcolor{comment}{ * THIS SOFTWARE IS PROVIDED BY THE COPYRIGHT HOLDERS AND CONTRIBUTORS}
\textcolor{comment}{ * "AS IS" AND ANY EXPRESS OR IMPLIED WARRANTIES, INCLUDING, BUT NOT LIMITED}
\textcolor{comment}{ * TO, THE IMPLIED WARRANTIES OF MERCHANTABILITY AND FITNESS FOR A PARTICULAR}
\textcolor{comment}{ * PURPOSE ARE DISCLAIMED. IN NO EVENT SHALL THE COPYRIGHT HOLDER OR}
\textcolor{comment}{ * CONTRIBUTORS BE LIABLE FOR ANY DIRECT, INDIRECT, INCIDENTAL, SPECIAL,}
\textcolor{comment}{ * EXEMPLARY, OR CONSEQUENTIAL DAMAGES (INCLUDING, BUT NOT LIMITED TO,}
\textcolor{comment}{ * PROCUREMENT OF SUBSTITUTE GOODS OR SERVICES; LOSS OF USE, DATA, OR}
\textcolor{comment}{ * PROFITS; OR BUSINESS INTERRUPTION) HOWEVER CAUSED AND ON ANY THEORY OF}
\textcolor{comment}{ * LIABILITY, WHETHER IN CONTRACT, STRICT LIABILITY, OR TORT (INCLUDING}
\textcolor{comment}{ * NEGLIGENCE OR OTHERWISE) ARISING IN ANY WAY OUT OF THE USE OF THIS}
\textcolor{comment}{ * SOFTWARE, EVEN IF ADVISED OF THE POSSIBILITY OF SUCH DAMAGE.}
\textcolor{comment}{ */}
\textcolor{preprocessor}{#include <stdint.h>}
\textcolor{preprocessor}{#include <stdlib.h>}
\textcolor{preprocessor}{#include <stdio.h>}

\textcolor{preprocessor}{#include <avr/io.h>}
\textcolor{preprocessor}{#include <avr/pgmspace.h>}

\textcolor{preprocessor}{#include <\hyperlink{tasks_8h}{tasks.h}>}
\textcolor{preprocessor}{#include <\hyperlink{xycontrol_8h}{xycontrol.h}>}
\textcolor{preprocessor}{#include <\hyperlink{time_8h}{time.h}>}
\textcolor{preprocessor}{#include <\hyperlink{uart_menu_8h}{uartMenu.h}>}
\textcolor{preprocessor}{#include <\hyperlink{serial_8h}{serial.h}>}
\textcolor{preprocessor}{#include <\hyperlink{acc_8h}{acc.h}>}
\textcolor{preprocessor}{#include <\hyperlink{gyro_8h}{gyro.h}>}
\textcolor{preprocessor}{#include <\hyperlink{mag_8h}{mag.h}>}
\textcolor{preprocessor}{#include <\hyperlink{motor_8h}{motor.h}>}
\textcolor{preprocessor}{#include <\hyperlink{orientation_8h}{orientation.h}>}
\textcolor{preprocessor}{#include <\hyperlink{xmem_8h}{xmem.h}>}
\textcolor{preprocessor}{#include <\hyperlink{error_8h}{error.h}>}

\textcolor{keywordtype}{void} ledTask(\textcolor{keywordtype}{void});
\textcolor{keywordtype}{void} printVoltage(\textcolor{keywordtype}{void});
\textcolor{keywordtype}{void} printRaw(\textcolor{keywordtype}{void});
\textcolor{keywordtype}{void} ramTest(\textcolor{keywordtype}{void});
\textcolor{keywordtype}{void} bluetoothTest(\textcolor{keywordtype}{void});

\textcolor{comment}{/*}
\textcolor{comment}{ * Strings for UART menu, stored in Flash.}
\textcolor{comment}{ */}
\textcolor{keywordtype}{char} PROGMEM voltageString[] = \textcolor{stringliteral}{"Battery Voltage"};
\textcolor{keywordtype}{char} PROGMEM sensorString[] = \textcolor{stringliteral}{"Raw Sensor Data"};
\textcolor{keywordtype}{char} PROGMEM ramString[] = \textcolor{stringliteral}{"Test external RAM"};
\textcolor{keywordtype}{char} PROGMEM bluetoothString[] = \textcolor{stringliteral}{"Test Bluetooth Module"};

\textcolor{keywordtype}{int} main(\textcolor{keywordtype}{void}) \{

    \textcolor{comment}{/*}
\textcolor{comment}{     * Initialize the System Timer, UART, TWI, SPI,}
\textcolor{comment}{     * ADC and the UART menu task for user or software}
\textcolor{comment}{     * interaction. Also enables interrupts!}
\textcolor{comment}{     * Also, the UART will be tied to stdin, stdout and stderr.}
\textcolor{comment}{     * This allows you to use stdio.h utilities like printf()}
\textcolor{comment}{     */}
    \hyperlink{group__xycontrol_ga2b3fb0734a2675e6dbdcb2c7665a708f}{xyInit}();
    printf(\textcolor{stringliteral}{"Initializing Hardware Test...\(\backslash\)n"});

    \textcolor{comment}{/*}
\textcolor{comment}{     * Initialize Hardware}
\textcolor{comment}{     */}
    \hyperlink{group__xycontrol_ga783aead7f97dd462a9af56b7fc3b228f}{xyLed}(\hyperlink{group__xycontrol_ggaadcb6002d2b42fdfe01490f730ab00a6a0ad916c7f80666dc88f6b5b22a72e742}{LED\_GREEN}, \hyperlink{group__xycontrol_gga51a69e0b98357e170e63bc843e2fd1c0afc0ca8cc6cbe215fd3f1ae6d40255b40}{LED\_OFF});
    \hyperlink{group__xycontrol_ga783aead7f97dd462a9af56b7fc3b228f}{xyLed}(\hyperlink{group__xycontrol_ggaadcb6002d2b42fdfe01490f730ab00a6ad80f13022b6d309268fadc7b1da89cb9}{LED\_RED}, \hyperlink{group__xycontrol_gga51a69e0b98357e170e63bc843e2fd1c0add01b80eb93658fb4cf7eb9aceb89a1d}{LED\_ON});
    \hyperlink{group__motor_gaa29e2982047be0f7afbb10c8d6f3f5c3}{motorInit}();
    \hyperlink{group__orientation_gaa5724492d0f54b41a8984cdde51d59df}{orientationInit}();

    \textcolor{comment}{/*}
\textcolor{comment}{     * Register Tasks in the Scheduler. A UART task}
\textcolor{comment}{     * is already registered...}
\textcolor{comment}{     */}
    \hyperlink{group__task_ga9a6ba4cb66e2fb7e3be42fb5b87fec6f}{addTask}(&ledTask); \textcolor{comment}{// Blink LED}

    \textcolor{comment}{/*}
\textcolor{comment}{     * Add commands for the UART menu}
\textcolor{comment}{     */}
    \hyperlink{group__uartmenu_gaba6c962adeaaeca40be02fb1098312ed}{addMenuCommand}(\textcolor{charliteral}{'b'}, bluetoothString, &bluetoothTest);
    \hyperlink{group__uartmenu_gaba6c962adeaaeca40be02fb1098312ed}{addMenuCommand}(\textcolor{charliteral}{'r'}, sensorString, &printRaw);
    \hyperlink{group__uartmenu_gaba6c962adeaaeca40be02fb1098312ed}{addMenuCommand}(\textcolor{charliteral}{'t'}, ramString, &ramTest);
    \hyperlink{group__uartmenu_gaba6c962adeaaeca40be02fb1098312ed}{addMenuCommand}(\textcolor{charliteral}{'v'}, voltageString, &printVoltage);

    printf(\textcolor{stringliteral}{"Hardware Test Initialized!\(\backslash\)n"});

    \textcolor{comment}{/*}
\textcolor{comment}{     * Execute all registered tasks, forever.}
\textcolor{comment}{     */}
    \textcolor{keywordflow}{for}(;;) \{
        \hyperlink{group__task_gabf4510e1aba7b08f11d447c2b530d661}{tasks}();
    \}

    \textcolor{keywordflow}{return} 0;
\}

\textcolor{keywordtype}{void} ledTask(\textcolor{keywordtype}{void}) \{
    \textcolor{comment}{/*}
\textcolor{comment}{     * Basic example of executing a task with a given frequency.}
\textcolor{comment}{     * last contains the last time this task was executed.}
\textcolor{comment}{     */}
    \textcolor{keyword}{static} \hyperlink{group__time_ga02ad034d26db2c14b7e295b0c50fc11d}{time\_t} last = 0;
    \textcolor{keywordflow}{if} ((\hyperlink{group__time_ga158463b7abdb2191a9a364bce1faac83}{getSystemTime}() - last) > 125) \{ \textcolor{comment}{// 125ms have passed}
        \hyperlink{group__xycontrol_ga783aead7f97dd462a9af56b7fc3b228f}{xyLed}(\hyperlink{group__xycontrol_ggaadcb6002d2b42fdfe01490f730ab00a6ae4fd580189cac85429ebfa5cb71cd772}{LED\_ALL}, \hyperlink{group__xycontrol_gga51a69e0b98357e170e63bc843e2fd1c0a1b3bca014fbbfe339c8e216d175bae2e}{LED\_TOGGLE}); \textcolor{comment}{// Do something...}
        last = \hyperlink{group__time_ga158463b7abdb2191a9a364bce1faac83}{getSystemTime}(); \textcolor{comment}{// Store new execution time}
    \}
\}

\textcolor{keywordtype}{void} printVoltage(\textcolor{keywordtype}{void}) \{
    printf(\textcolor{stringliteral}{"Battery: %fV\(\backslash\)n"}, \hyperlink{group__xycontrol_ga97874cf2a7f8e6964188b54fe85084a6}{getVoltage}());
\}

\textcolor{keywordtype}{void} printRaw(\textcolor{keywordtype}{void}) \{
    \hyperlink{struct_vector3f}{Vector3f} v;
    \hyperlink{group__acc_ga4dd55defcab17af4ecc29562a5a28ab3}{accRead}(&v);
    printf(\textcolor{stringliteral}{"Ax: %f Ay: %f Az: %f\(\backslash\)n"}, v.\hyperlink{struct_vector3f_af88b946fb90d5f08b5fb740c70e98c10}{x}, v.\hyperlink{struct_vector3f_ab927965981178aa1fba979a37168db2a}{y}, v.\hyperlink{struct_vector3f_ab3e6ed577a7c669c19de1f9c1b46c872}{z});
    \hyperlink{group__gyro_gab90a6ac7c268152edb186ee699462fd8}{gyroRead}(&v);
    printf(\textcolor{stringliteral}{"Gx: %f Gy: %f Gz: %f\(\backslash\)n"}, v.\hyperlink{struct_vector3f_af88b946fb90d5f08b5fb740c70e98c10}{x}, v.\hyperlink{struct_vector3f_ab927965981178aa1fba979a37168db2a}{y}, v.\hyperlink{struct_vector3f_ab3e6ed577a7c669c19de1f9c1b46c872}{z});
    \hyperlink{group__mag_gacc0c83a48498170ef36451db2c684abb}{magRead}(&v);
    printf(\textcolor{stringliteral}{"Mx: %f My: %f Mz: %f\(\backslash\)n"}, v.\hyperlink{struct_vector3f_af88b946fb90d5f08b5fb740c70e98c10}{x}, v.\hyperlink{struct_vector3f_ab927965981178aa1fba979a37168db2a}{y}, v.\hyperlink{struct_vector3f_ab3e6ed577a7c669c19de1f9c1b46c872}{z});
\}

\textcolor{preprocessor}{#define CHECKSIZE 53248 // 52KB}
\textcolor{preprocessor}{}
\textcolor{keywordtype}{void} ramTest(\textcolor{keywordtype}{void}) \{
    uint8\_t *blocks[\hyperlink{group__xmem_ga1ed280cb3dd0a4a03aeda6aaccc180d3}{MEMBANKS}];
    uint8\_t oldBank = \hyperlink{group__xmem_ga575f63170f6fc636556f8d955cbd42cd}{xmemGetBank}();

    printf(\textcolor{stringliteral}{"Allocating Test Memory...\(\backslash\)n"});
    \textcolor{keywordflow}{for} (uint8\_t i = 0; i < \hyperlink{group__xmem_ga1ed280cb3dd0a4a03aeda6aaccc180d3}{MEMBANKS}; i++) \{
        \hyperlink{group__xmem_ga619fa66b9f38be684f4331951fc91730}{xmemSetBank}(i);
        blocks[i] = (uint8\_t *)malloc(CHECKSIZE);
        \textcolor{keywordflow}{if} (blocks[i] == NULL) \{
            printf(\textcolor{stringliteral}{"  Error: Couldn't allocate %liKB in Bank %i!\(\backslash\)n"}, (CHECKSIZE / 1024), i);
        \} \textcolor{keywordflow}{else} \{
            printf(\textcolor{stringliteral}{"  Bank %i ready!\(\backslash\)n"}, i);
        \}
    \}
    printf(\textcolor{stringliteral}{"Filling with data...\(\backslash\)n"});
    \textcolor{keywordflow}{for} (uint8\_t i = 0; i < \hyperlink{group__xmem_ga1ed280cb3dd0a4a03aeda6aaccc180d3}{MEMBANKS}; i++) \{
        \hyperlink{group__xmem_ga619fa66b9f38be684f4331951fc91730}{xmemSetBank}(i);
        \textcolor{keywordflow}{for} (uint16\_t j = 0; j < CHECKSIZE; j++) \{
            blocks[i][j] = (j & 0xFF);
        \}
        printf(\textcolor{stringliteral}{"  Filled Bank %i!\(\backslash\)n"}, i);
    \}
    printf(\textcolor{stringliteral}{"Checking data...\(\backslash\)n"});
    \textcolor{keywordflow}{for} (uint8\_t i = 0; i < \hyperlink{group__xmem_ga1ed280cb3dd0a4a03aeda6aaccc180d3}{MEMBANKS}; i++) \{
        \hyperlink{group__xmem_ga619fa66b9f38be684f4331951fc91730}{xmemSetBank}(i);
        uint8\_t error = 0;
        \textcolor{keywordflow}{for} (uint16\_t j = 0; ((j < CHECKSIZE) && (!error)); j++) \{
            \textcolor{keywordflow}{if} (blocks[i][j] != (j & 0xFF)) \{
                printf(\textcolor{stringliteral}{"  Error at %i in %i!\(\backslash\)n"}, j, i);
                error = 1;
            \}
        \}
        \textcolor{keywordflow}{if} (!error) \{
            printf(\textcolor{stringliteral}{"  Bank %i okay!\(\backslash\)n"}, i);
        \}
    \}
    printf(\textcolor{stringliteral}{"Freeing memory...\(\backslash\)n"});
    \textcolor{keywordflow}{for} (uint8\_t i = 0; i < \hyperlink{group__xmem_ga1ed280cb3dd0a4a03aeda6aaccc180d3}{MEMBANKS}; i++) \{
        \hyperlink{group__xmem_ga619fa66b9f38be684f4331951fc91730}{xmemSetBank}(i);
        free(blocks[i]);
    \}
    printf(\textcolor{stringliteral}{"Finished!\(\backslash\)n"});

    \hyperlink{group__xmem_ga619fa66b9f38be684f4331951fc91730}{xmemSetBank}(oldBank);
\}

\textcolor{keywordtype}{void} bluetoothTest(\textcolor{keywordtype}{void}) \{
    printf(\textcolor{stringliteral}{"Please disconnect, wait 10s, then reconnect!\(\backslash\)n"});
    printf(\textcolor{stringliteral}{"All data will be logged, then printed after 15s.\(\backslash\)n"});
    \hyperlink{group__time_ga02ad034d26db2c14b7e295b0c50fc11d}{time\_t} start = \hyperlink{group__time_ga158463b7abdb2191a9a364bce1faac83}{getSystemTime}();
    \textcolor{keywordflow}{while} ((\hyperlink{group__time_ga158463b7abdb2191a9a364bce1faac83}{getSystemTime}() - start) <= 15000); \textcolor{comment}{// Wait}
    \textcolor{keywordflow}{while} (\hyperlink{group__uart_ga266a54dcf3c4b85d92bf6b16bdcb5069}{serialHasChar}(\hyperlink{group__uart_ga3f30897fa8435dc9811642367a328be8}{BLUETOOTH})) \{ \textcolor{comment}{// Check}
        \hyperlink{group__uart_ga388583adaa7db4fad121b6454668b347}{serialWrite}(\hyperlink{group__uart_ga779bf099075a999d1074357fccbd466b}{USB}, \hyperlink{group__uart_gaa9d6e44600b215154c3f66193df151f6}{serialGet}(\hyperlink{group__uart_ga3f30897fa8435dc9811642367a328be8}{BLUETOOTH}));
    \}
    printf(\textcolor{stringliteral}{"\(\backslash\)n\(\backslash\)nDone!\(\backslash\)n"});
\}
\end{DoxyCodeInclude}

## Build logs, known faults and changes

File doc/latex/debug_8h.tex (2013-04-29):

\hypertarget{debug_8h}{\section{include/debug.h File Reference}
\label{debug_8h}\index{include/debug.\-h@{include/debug.\-h}}
}

Debug and Assert Header and Implementation.  

{\ttfamily \#include $<$avr/wdt.\-h$>$}\\*
{\ttfamily \#include $<$serial.\-h$>$}\\*
{\ttfamily \#include $<$stdio.\-h$>$}\\*
\subsection*{Macros}
\begin{DoxyCompactItemize}
\item 
\#define \hyperlink{group__debug_ga19525f7b34cac5693e8cd76d113de4ea}{D\-E\-B\-U\-G\-O\-U\-T}(x)~printf(\char`\"{}!\%s\textbackslash{}n\char`\"{}, x)
\begin{DoxyCompactList}\small\item\em Debug Output Function. \end{DoxyCompactList}\item 
\#define \hyperlink{group__debug_ga9dfd1281735240dcb36d5f605013d40e}{A\-S\-S\-E\-R\-T\-F\-U\-N\-C}(x)
\begin{DoxyCompactList}\small\item\em Simple Assert Implementation. \end{DoxyCompactList}\item 
\#define \hyperlink{group__debug_gaf576bf8ffa22a44e53018c67095ffbf0}{assert}(x)~\hyperlink{group__debug_ga9dfd1281735240dcb36d5f605013d40e}{A\-S\-S\-E\-R\-T\-F\-U\-N\-C}(x)
\begin{DoxyCompactList}\small\item\em Enable \hyperlink{group__debug_gaf576bf8ffa22a44e53018c67095ffbf0}{assert()} \end{DoxyCompactList}\item 
\#define \hyperlink{group__debug_gada1787bea8c10cd89775d6918f6fd324}{debug\-Print}(ignore)
\begin{DoxyCompactList}\small\item\em Disable \hyperlink{group__debug_gada1787bea8c10cd89775d6918f6fd324}{debug\-Print()} \end{DoxyCompactList}\end{DoxyCompactItemize}

\subsection{Detailed Description}
Debug and Assert Header and Implementation. 

Definition in file \hyperlink{debug_8h_source}{debug.\-h}.

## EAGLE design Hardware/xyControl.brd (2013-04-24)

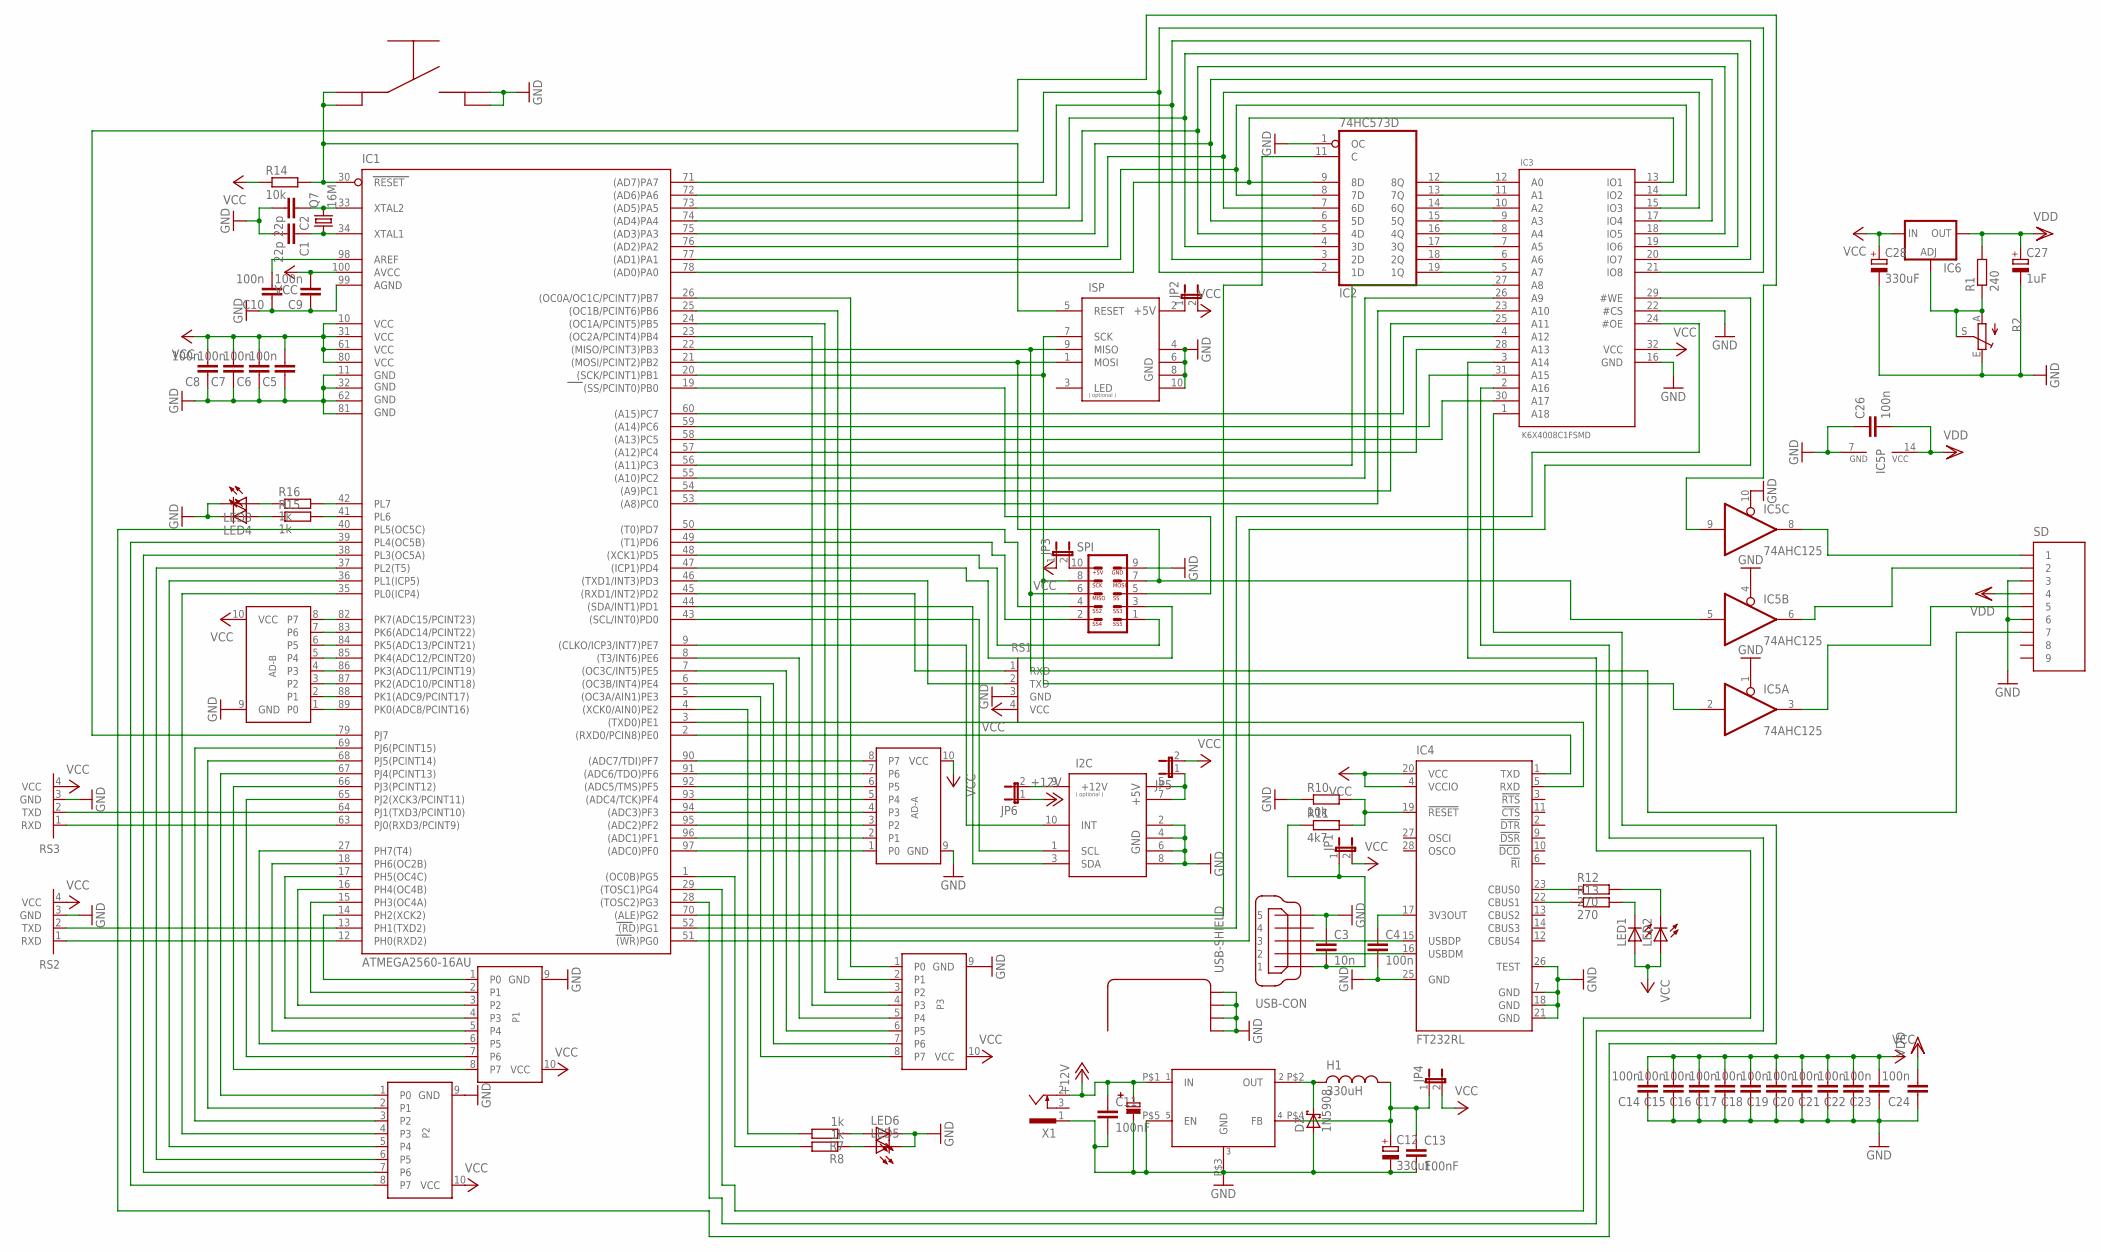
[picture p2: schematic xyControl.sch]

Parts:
AD-A: PORT; ML10
AD-B: PORT; ML10
C1, C2: 22p; C0603K
C3: 10n; C0603K
C4, C5, C6, C7, C8, C9, C10, C14, C15, C16, C17, C18, C19, C20, C21, C22, C23, C24, C26: 100n; C0603K
C11, C13: 100nF; C0603K
C12: 330uF; PANASONIC_F
C25: 100uF; ELKO_SMD_6.5
C27: 1uF; E2,5-6
C28: 330uF; E5-10,5
D2: 1N5908; C4111-15
H1: 330uH; PISR
I2C: I2C; ML10
IC1: ATMEGA2560-16AU; TQFP100
IC2: 74HC573D; SO20W
IC3: K6X4008C1FSMD; SOP-32
IC4: FT232RL; SSOP28
IC5: 74AHC125; SO14
IC6: LM317L; 317L
ISP: AVR-ISP; ML10
JP1, JP2, JP3, JP4, JP5, JP6: JP1E; JP1
LED1, LED2, LED3, LED4, LED5, LED6: LEDCHIP-LED0603; CHIP-LED0603
LM2576-5: LM2576; TO-220
P1, P2, P3: PORT; ML10
Q7: 16M; HC49/S
R1: 240; R0603
R2: POT_TRIM_EU-ST10; POT_ST10
R7, R8, R15, R16: 1k; R0603
R10, R14: 10k; R0603
R11: 4k7; R0603
R12, R13: 270; R0603
RS1, RS2, RS3: RS232_TTL; 1X04
SD: FPS009-30003; FPS009-3003
SPI: SPISTECKER; ML10
T1: 0-XYTHOBUZ_TASTER; 0-XYTHOBUZ_SMDTASTER
USB: 1_USER_USB-B-MINI-SMD
X1: CON-CONRAD_733980-62

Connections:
+12V: C11.1, C25.P$2, JP6.1, LM2576-5.P$1 (IN), X1.2
GND: AD-A.9 (GND), AD-B.9 (GND), C1.2, C2.2, C3.1, C4.2, C5.1, C6.1, C7.1, C8.1, C9.1, C10.1, C11.2, C12.-, C13.2, C14.1, C15.1, C16.1, C17.1, C18.1, C19.1, C20.1, C21.1, C22.1, C23.1, C24.1, C25.P$1, C26.1, C27.-, C28.-, D2.A, I2C.2 (GND), I2C.4 (GND), I2C.6 (GND), I2C.8 (GND), IC1.11 (GND), IC1.32 (GND1), IC1.62 (GND2), IC1.81 (GND3), IC1.99 (AGND), IC2.1 (OC), IC2.10 (GND), IC3.16 (GND), IC3.22 (#CS), IC4.7 (GND), IC4.18 (GND), IC4.21 (GND), IC4.25 (GND), IC4.26 (TEST), IC5.1 (OE), IC5.4 (OE), IC5.7 (GND), IC5.10 (OE), ISP.4 (GND), ISP.6 (GND), ISP.8 (GND), ISP.10 (GND), LED3.C, LED4.C, LED5.C, LED6.C, LM2576-5.P$3 (GND), LM2576-5.P$5 (EN), P1.9 (GND), P2.9 (GND), P3.9 (GND), R2.E, R10.1, RS1.3 (GND), RS2.3 (GND), RS3.3 (GND), SD.3, SD.6, SPI.9, T1.B, T1.B2, USB.5, USB.M1 (S1), USB.M2 (S2), USB.M3 (S3), USB.M4 (S4), X1.1
unnamed: IC1.78 ((AD0)PA0), IC2.9 (8D), IC3.13 (IO1)
unnamed: IC1.77 ((AD1)PA1), IC2.8 (7D), IC3.14 (IO2)
unnamed: IC1.76 ((AD2)PA2), IC2.7 (6D), IC3.15 (IO3)
unnamed: IC1.75 ((AD3)PA3), IC2.6 (5D), IC3.17 (IO4)
unnamed: IC1.74 ((AD4)PA4), IC2.5 (4D), IC3.18 (IO5)
unnamed: IC1.73 ((AD5)PA5), IC2.4 (3D), IC3.19 (IO6)
unnamed: IC1.72 ((AD6)PA6), IC2.3 (2D), IC3.20 (IO7)
unnamed: IC1.71 ((AD7)PA7), IC2.2 (1D), IC3.21 (IO8)
unnamed: IC2.12 (8Q), IC3.12 (A0)
unnamed: IC2.13 (7Q), IC3.11 (A1)
unnamed: IC2.14 (6Q), IC3.10 (A2)
unnamed: IC2.15 (5Q), IC3.9 (A3)
unnamed: IC2.16 (4Q), IC3.8 (A4)
unnamed: IC2.17 (3Q), IC3.7 (A5)
unnamed: IC2.18 (2Q), IC3.6 (A6)
unnamed: IC2.19 (1Q), IC3.5 (A7)
unnamed: IC1.2 ((RXD0/PCIN8)PE0), IC4.1 (TXD)
unnamed: IC1.3 ((TXD0)PE1), IC4.5 (RXD)
unnamed: ISP.2 (+5V), JP2.1
unnamed: JP3.2, SPI.10
unnamed: IC1.19 ((SS/PCINT0)PB0), SPI.5
unnamed: IC1.50 ((T0)PD7), SPI.4
unnamed: IC1.49 ((T1)PD6), SPI.2
unnamed: IC1.48 ((XCK1)PD5), SPI.1
unnamed: IC1.53 ((A8)PC0), IC3.23 (A10)
unnamed: IC1.54 ((A9)PC1), IC3.25 (A11)
unnamed: IC1.55 ((A10)PC2), IC3.26 (A9)
unnamed: IC1.56 ((A11)PC3), IC3.27 (A8)
unnamed: IC1.57 ((A12)PC4), IC3.28 (A13)
unnamed: IC1.58 ((A13)PC5), IC3.30 (A17)
unnamed: IC1.59 ((A14)PC6), IC3.31 (A15)
unnamed: IC1.60 ((A15)PC7), IC3.4 (A12)
unnamed: IC1.47 ((ICP1)PD4), SPI.3
unnamed: IC1.70 ((ALE)PG2), IC2.11 (C)
unnamed: IC1.52 ((RD)PG1), IC3.24 (#OE)
unnamed: IC1.51 ((WR)PG0), IC3.29 (#WE)
unnamed: IC1.20 ((SCK/PCINT1)PB1), IC5.2 (I), ISP.7 (SCK), SPI.8
unnamed: IC1.22 ((MISO/PCINT3)PB3), ISP.9 (MISO), SD.7, SPI.6
unnamed: IC1.21 ((MOSI/PCINT2)PB2), IC5.5 (I), ISP.1 (MOSI), SPI.7
unnamed: IC1.30 (RESET), ISP.5 (RESET), R14.2, T1.A, T1.A2
unnamed: I2C.5 (+5V), I2C.7 (+5V), JP5.1
unnamed: I2C.1 (SCL), IC1.43 ((SCL/INT0)PD0)
unnamed: I2C.3 (SDA), IC1.44 ((SDA/INT1)PD1)
unnamed: I2C.10 (INT), IC1.9 ((CLKO/ICP3/INT7)PE7)
unnamed: IC1.46 ((TXD1/INT3)PD3), RS1.2 (TXD)
unnamed: IC1.45 ((RXD1/INT2)PD2), RS1.1 (RXD)
unnamed: IC1.64 (PJ1(TXD3/PCINT10)), RS3.2 (TXD)
unnamed: IC1.63 (PJ0(RXD3/PCINT9)), RS3.1 (RXD)
unnamed: IC1.13 (PH1(TXD2)), RS2.2 (TXD)
unnamed: IC1.12 (PH0(RXD2)), RS2.1 (RXD)
unnamed: AD-A.8 (P7), IC1.90 ((ADC7/TDI)PF7)
unnamed: AD-A.7 (P6), IC1.91 ((ADC6/TDO)PF6)
unnamed: AD-A.6 (P5), IC1.92 ((ADC5/TMS)PF5)
unnamed: AD-A.1 (P0), IC1.97 ((ADC0)PF0)
unnamed: AD-A.2 (P1), IC1.96 ((ADC1)PF1)
unnamed: AD-A.3 (P2), IC1.95 ((ADC2)PF2)
unnamed: AD-A.4 (P3), IC1.94 ((ADC3)PF3)
unnamed: AD-A.5 (P4), IC1.93 ((ADC4/TCK)PF4)
unnamed: IC1.28 ((TOSC2)PG3), IC3.2 (A16)
unnamed: C1.1, IC1.34 (XTAL1), Q7.1
unnamed: AD-B.1 (P0), IC1.89 (PK0(ADC8/PCINT16))
unnamed: AD-B.2 (P1), IC1.88 (PK1(ADC9/PCINT17))
unnamed: AD-B.3 (P2), IC1.87 (PK2(ADC10/PCINT18))
unnamed: AD-B.4 (P3), IC1.86 (PK3(ADC11/PCINT19))
unnamed: AD-B.5 (P4), IC1.85 (PK4(ADC12/PCINT20))
unnamed: AD-B.6 (P5), IC1.84 (PK5(ADC13/PCINT21))
unnamed: AD-B.7 (P6), IC1.83 (PK6(ADC14/PCINT22))
unnamed: AD-B.8 (P7), IC1.82 (PK7(ADC15/PCINT23))
unnamed: IC1.29 ((TOSC1)PG4), IC3.3 (A14)
unnamed: LED6.A, R7.1
unnamed: LED5.A, R8.1
unnamed: IC4.16 (USBDM), USB.2
unnamed: C4.1, IC4.17 (3V3OUT)
unnamed: IC4.15 (USBDP), USB.3
unnamed: IC4.19 (!RESET), R10.2, R11.2
unnamed: IC1.79 (PJ7), IC5.9 (I)
unnamed: IC5.3 (O), SD.5
unnamed: IC5.6 (O), SD.2
unnamed: IC5.8 (O), SD.1
unnamed: IC4.23 (CBUS0), R12.1
unnamed: C3.2, JP1.1, R11.1, USB.1
unnamed: IC4.22 (CBUS1), R13.1
unnamed: IC6.1 (ADJ), R1.1, R2.A, R2.S
unnamed: LED1.C, R13.2
unnamed: LED2.C, R12.2
unnamed: C2.1, IC1.33 (XTAL2), Q7.2
unnamed: D2.C, H1.P$1, LM2576-5.P$2 (OUT)
unnamed: C12.+, C13.1, H1.P$2, JP4.1, LM2576-5.P$4 (FB)
unnamed: IC1.14 (PH2(XCK2)), P1.1 (P0)
unnamed: IC1.15 (PH3(OC4A)), P1.2 (P1)
unnamed: I2C.9 (+12V), JP6.2
unnamed: IC1.16 (PH4(OC4B)), P1.3 (P2)
unnamed: C10.2, IC1.98 (AREF)
unnamed: IC1.17 (PH5(OC4C)), P1.4 (P3)
unnamed: IC1.18 (PH6(OC2B)), P1.5 (P4)
unnamed: IC1.27 (PH7(T4)), P1.6 (P5)
unnamed: IC1.65 (PJ2(XCK3/PCINT11)), P1.7 (P6)
unnamed: IC1.66 (PJ3(PCINT12)), P1.8 (P7)
unnamed: IC1.67 (PJ4(PCINT13)), P2.1 (P0)
unnamed: IC1.68 (PJ5(PCINT14)), P2.2 (P1)
unnamed: IC1.69 (PJ6(PCINT15)), P2.3 (P2)
unnamed: IC1.35 (PL0(ICP4)), P2.4 (P3)
unnamed: IC1.36 (PL1(ICP5)), P2.5 (P4)
unnamed: IC1.37 (PL2(T5)), P2.6 (P5)
unnamed: IC1.38 (PL3(OC5A)), P2.7 (P6)
unnamed: IC1.39 (PL4(OC5B)), P2.8 (P7)
unnamed: IC1.40 (PL5(OC5C)), IC3.1 (A18)
unnamed: IC1.41 (PL6), R15.2
unnamed: IC1.42 (PL7), R16.2
unnamed: LED4.A, R15.1
unnamed: LED3.A, R16.1
unnamed: IC1.1 ((OC0B)PG5), R8.2
unnamed: IC1.4 ((XCK0/AIN0)PE2), R7.2
unnamed: IC1.5 ((OC3A/AIN1)PE3), P3.8 (P7)
unnamed: IC1.6 ((OC3B/INT4)PE4), P3.7 (P6)
unnamed: IC1.7 ((OC3C/INT5)PE5), P3.6 (P5)
unnamed: IC1.8 ((T3/INT6)PE6), P3.5 (P4)
unnamed: IC1.23 ((OC2A/PCINT4)PB4), P3.4 (P3)
unnamed: IC1.24 ((OC1A/PCINT5)PB5), P3.3 (P2)
unnamed: IC1.25 ((OC1B/PCINT6)PB6), P3.2 (P1)
unnamed: IC1.26 ((OC0A/OC1C/PCINT7)PB7), P3.1 (P0)
VCC: AD-A.10 (VCC), AD-B.10 (VCC), C5.2, C6.2, C7.2, C8.2, C9.2, C14.2, C15.2, C16.2, C17.2, C18.2, C19.2, C20.2, C21.2, C22.2, C23.2, C28.+, IC1.10 (VCC), IC1.31 (VCC1), IC1.61 (VCC2), IC1.80 (VCC3), IC1.100 (AVCC), IC2.20 (VCC), IC3.32 (VCC), IC4.4 (VCCIO), IC4.20 (VCC), IC6.3 (IN), JP1.2, JP2.2, JP3.1, JP4.2, JP5.2, LED1.A, LED2.A, P1.10 (VCC), P2.10 (VCC), P3.10 (VCC), R14.1, RS1.4 (VCC), RS2.4 (VCC), RS3.4 (VCC)
VDD: C24.2, C26.2, C27.+, IC5.14 (VCC), IC6.2 (OUT), R1.2, SD.4

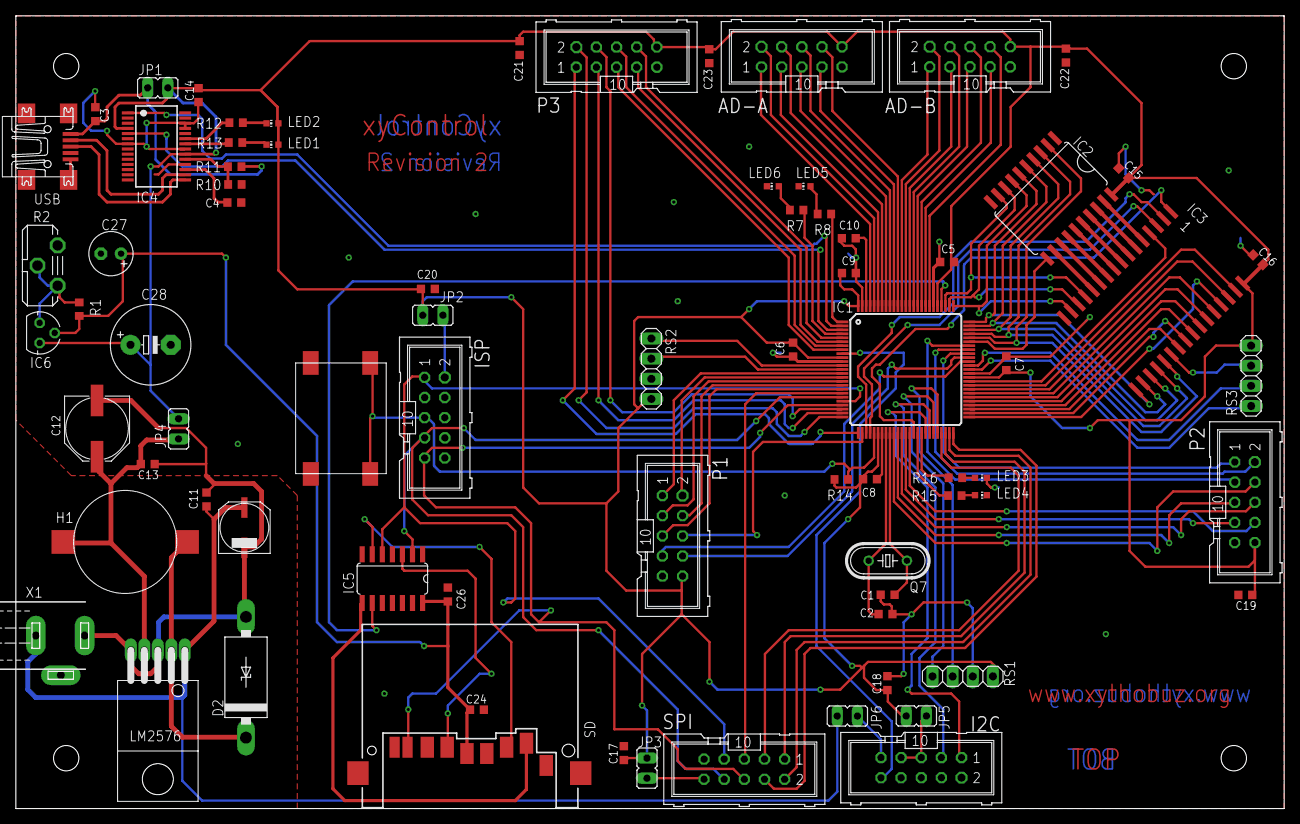
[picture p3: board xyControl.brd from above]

Board: 2 copper layers, 160.0 x 100.0 mm, 76 parts (0 on the bottom side), 125 nets.

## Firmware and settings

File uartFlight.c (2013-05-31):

/*
 * uartFlight.c
 *
 * Copyright (c) 2013, Thomas Buck <xythobuz@me.com>
 * All rights reserved.
 *
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
 * - Redistributions in binary form must reproduce the above copyright
 *   notice, this list of conditions and the following disclaimer in the
 *   documentation and/or other materials provided with the distribution.
 *
 * THIS SOFTWARE IS PROVIDED BY THE COPYRIGHT HOLDERS AND CONTRIBUTORS
 * "AS IS" AND ANY EXPRESS OR IMPLIED WARRANTIES, INCLUDING, BUT NOT LIMITED
 * TO, THE IMPLIED WARRANTIES OF MERCHANTABILITY AND FITNESS FOR A PARTICULAR
 * PURPOSE ARE DISCLAIMED. IN NO EVENT SHALL THE COPYRIGHT HOLDER OR
 * CONTRIBUTORS BE LIABLE FOR ANY DIRECT, INDIRECT, INCIDENTAL, SPECIAL,
 * EXEMPLARY, OR CONSEQUENTIAL DAMAGES (INCLUDING, BUT NOT LIMITED TO,
 * PROCUREMENT OF SUBSTITUTE GOODS OR SERVICES; LOSS OF USE, DATA, OR
 * PROFITS; OR BUSINESS INTERRUPTION) HOWEVER CAUSED AND ON ANY THEORY OF
 * LIABILITY, WHETHER IN CONTRACT, STRICT LIABILITY, OR TORT (INCLUDING
 * NEGLIGENCE OR OTHERWISE) ARISING IN ANY WAY OUT OF THE USE OF THIS
 * SOFTWARE, EVEN IF ADVISED OF THE POSSIBILITY OF SUCH DAMAGE.
 */
#include <stdint.h>
#include <stdlib.h>
#include <stdio.h>
#include <avr/io.h>
#include <avr/pgmspace.h>

#define DEBUG 1

#include <debug.h>
#include <tasks.h>
#include <error.h>
#include <xycontrol.h>
#include <time.h>
#include <uartMenu.h>
#include <serial.h>
#include <acc.h>
#include <gyro.h>
#include <mag.h>
#include <motor.h>
#include <orientation.h>
#include <pid.h>
#include <set.h>

/** \example uartFlight.c */

#define MAXANGLE 45
#define ANGLESTEP 10
#define MAXMOTOR 255
#define MOTORSTEP 10
#define QUADFREQ 100
#define STATUSFREQ 10

#define QUADDELAY (1000 / QUADFREQ)
#define STATUSDELAY (1000 / STATUSFREQ)

void flightTask(void);
void statusTask(void);
void controlToggle(void);
void motorToggle(void);
void motorUp(void);
void motorDown(void);
void motorForward(void);
void motorBackward(void);
void motorLeft(void);
void motorRight(void);
void parameterChange(void);
void silent(void);
void printRaw(void);

char PROGMEM motorToggleString[] = "Motor On/Off";
char PROGMEM motorUpString[] = "Up";
char PROGMEM motorDownString[] = "Down";
char PROGMEM motorLeftString[] = "Left";
char PROGMEM motorRightString[] = "Right";
char PROGMEM motorForwardString[] = "Forwards";
char PROGMEM motorBackwardString[] = "Backwards";
char PROGMEM controlToggleString[] = "Toggle PID";
char PROGMEM parameterChangeString[] = "Change PID Params";
char PROGMEM zeroString[] = "Angles to Zero";
char PROGMEM silentString[] = "Toggle Status Output";
char PROGMEM sensorString[] = "Raw Sensor Data";

#define STATE_MOTOR (1 << 0) // 1 -> Motor On
#define STATE_PID (1 << 1) // 1 -> PID enabled
#define STATE_OUTPUT (1 << 2) // 1 -> No Status Output
uint8_t state = 0;

uint8_t speed = 10;
int16_t targetRoll = 0;
int16_t targetPitch = 0;

uint32_t sumFlightTask = 0, countFlightTask = 0;

int main(void) {
    xyInit();
    pidInit();
    motorInit();
    orientationInit();

    debugPrint("Initialized Hardware");

    addTask(&flightTask);
    addTask(&statusTask);

    addMenuCommand('m', motorToggleString, &motorToggle);
    addMenuCommand('w', motorForwardString, &motorForward);
    addMenuCommand('a', motorLeftString, &motorLeft);
    addMenuCommand('s', motorBackwardString, &motorBackward);
    addMenuCommand('d', motorRightString, &motorRight);
    addMenuCommand('x', motorUpString, &motorUp);
    addMenuCommand('y', motorDownString, &motorDown);
    addMenuCommand('p', controlToggleString, &controlToggle);
    addMenuCommand('n', parameterChangeString, &parameterChange);
    addMenuCommand('z', zeroString, &zeroOrientation);
    addMenuCommand('o', silentString, &silent);
    addMenuCommand('r', sensorString, &printRaw);

    xyLed(LED_RED, LED_OFF);
    xyLed(LED_GREEN, LED_ON);

    debugPrint("Starting Tasks");

    for(;;) {
        tasks();
    }

    return 0;
}

void flightTask(void) {
    static time_t last = 100; // Don't begin immediately
    if ((getSystemTime() - last) >= QUADDELAY) {
        last = getSystemTime();
        Error e = orientationTask();
        REPORTERROR(e);
        if (state & STATE_PID) {
            pidTask();
        } else {
            pidOutput[0] = pidOutput[1] = 0;
        }
        setTask();
        motorTask();

        uint32_t diff = getSystemTime() - last;
        if (++countFlightTask >= QUADFREQ) {
            countFlightTask = 1;
            sumFlightTask = diff;
        } else {
            sumFlightTask += diff;
        }
    }
}

void statusTask(void) {
    static time_t last = 100; // Don't begin immediately
    static uint32_t lastDuration = 0;
    if (((getSystemTime() - last) >= STATUSDELAY) && (!(state & STATE_OUTPUT))) {
        last = getSystemTime();
        printf("p%.2f %.2f %.2f\n", orientation.vPitch, orientation.vRoll, orientation.vYaw);
        printf("q%li %li\n", sumFlightTask / countFlightTask, lastDuration);
        printf("r%.2f %.2f\n", pidStates[0].intMin, pidStates[0].intMax);
        printf("s%.2f %.2f\n", pidStates[0].outMin, pidStates[0].outMax);
        printf("t%.3f %.3f %.3f\n", pidStates[0].kp, pidStates[0].ki, pidStates[0].kd);
        printf("u%.2f %.2f\n", pidOutput[PITCH], pidOutput[ROLL]);
        printf("v%i %i %i %i\n", motorSpeed[0], motorSpeed[1], motorSpeed[2], motorSpeed[3]);
        printf("w%.2f\n", orientation.pitch);
        printf("x%.2f\n", orientation.roll);
        printf("y%.2f\n", orientation.yaw);
        printf("z%.2f\n", getVoltage());
        lastDuration = getSystemTime() - last;
    }
}

void controlToggle(void) {
    if (state & STATE_PID) {
        state &= ~STATE_PID;
        printf("PID Off!\n");
    } else {
        state |= STATE_PID;
        printf("PID On!\n");
    }
}

void motorToggle(void) {
    if (state & STATE_MOTOR) {
        state &= ~STATE_MOTOR;
        baseSpeed = 0;
        printf("Motor Off!\n");
    } else {
        state |= STATE_MOTOR;
        baseSpeed = speed = 10;
        printf("Motor On!\n");
    }
}

void motorUp(void) {
    if (speed <= (MAXMOTOR - MOTORSTEP)) {
        if (state & STATE_MOTOR) {
            speed += MOTORSTEP;
            baseSpeed = speed;
            printf("Throttle up to %i\n", speed);
        }
    }
}

void motorDown(void) {
    if (speed >= MOTORSTEP) {
        if (state & STATE_MOTOR) {
            speed -= MOTORSTEP;
            baseSpeed = speed;
            printf("Throttle down to %i\n", speed);
        }
    }
}

void motorForward(void) {
    if (targetPitch >= (-1 * (MAXANGLE - ANGLESTEP))) {
        targetPitch -= ANGLESTEP;
        pidTarget[PITCH] = targetPitch;
        printf("Pitch Forward %i\n", targetPitch);
    }
}

void motorBackward(void) {
    if (targetPitch <= (MAXANGLE - ANGLESTEP)) {
        targetPitch += ANGLESTEP;
        pidTarget[PITCH] = targetPitch;
        printf("Pitch Backwards %i\n", targetPitch);
    }
}

void motorLeft(void) {
    if (targetRoll <= (MAXANGLE - ANGLESTEP)) {
        targetRoll += ANGLESTEP;
        pidTarget[ROLL] = targetRoll;
        printf("Roll Left %i\n", targetRoll);
    }
}

void motorRight(void) {
    if (targetRoll >= (-1 * (MAXANGLE - ANGLESTEP))) {
        targetRoll -= ANGLESTEP;
        pidTarget[ROLL] = targetRoll;
        printf("Roll Right %i\n", targetRoll);
    }
}

void parameterChange(void) {
    double p, i, d, min, max, iMin, iMax;
    int c = scanf("%lf %lf %lf %lf %lf %lf %lf", &p, &i, &d, &min, &max, &iMin, &iMax);
    if (c == 7) {
        pidSet(&pidStates[0], p, i, d, min, max, iMin, iMax);
        pidSet(&pidStates[1], p, i, d, min, max, iMin, iMax);
    } else {
        printf("Only got %i (%lf %lf %lf %lf %lf %lf %lf)!\n", c, p, i, d, min, max, iMin, iMax);
    }
}

void silent(void) {
    if (state & STATE_OUTPUT) {
        // Currently disabled, bit set
        state &= ~STATE_OUTPUT; // Unset Bit
    } else {
        // Currently enabled
        state |= STATE_OUTPUT; // Set Bit
    }
}

void printRaw(void) {
    Vector3f v;
    accRead(&v);
    printf("Ax: %f Ay: %f Az: %f\n", v.x, v.y, v.z);
    gyroRead(&v);
    printf("Gx: %f Gy: %f Gz: %f\n", v.x, v.y, v.z);
    magRead(&v);
    printf("Mx: %f My: %f Mz: %f\n", v.x, v.y, v.z);
}

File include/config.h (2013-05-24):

/*
 * config.h
 *
 * Copyright (c) 2013, Thomas Buck <xythobuz@me.com>
 * All rights reserved.
 *
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
 * - Redistributions in binary form must reproduce the above copyright
 *   notice, this list of conditions and the following disclaimer in the
 *   documentation and/or other materials provided with the distribution.
 *
 * THIS SOFTWARE IS PROVIDED BY THE COPYRIGHT HOLDERS AND CONTRIBUTORS
 * "AS IS" AND ANY EXPRESS OR IMPLIED WARRANTIES, INCLUDING, BUT NOT LIMITED
 * TO, THE IMPLIED WARRANTIES OF MERCHANTABILITY AND FITNESS FOR A PARTICULAR
 * PURPOSE ARE DISCLAIMED. IN NO EVENT SHALL THE COPYRIGHT HOLDER OR
 * CONTRIBUTORS BE LIABLE FOR ANY DIRECT, INDIRECT, INCIDENTAL, SPECIAL,
 * EXEMPLARY, OR CONSEQUENTIAL DAMAGES (INCLUDING, BUT NOT LIMITED TO,
 * PROCUREMENT OF SUBSTITUTE GOODS OR SERVICES; LOSS OF USE, DATA, OR
 * PROFITS; OR BUSINESS INTERRUPTION) HOWEVER CAUSED AND ON ANY THEORY OF
 * LIABILITY, WHETHER IN CONTRACT, STRICT LIABILITY, OR TORT (INCLUDING
 * NEGLIGENCE OR OTHERWISE) ARISING IN ANY WAY OUT OF THE USE OF THIS
 * SOFTWARE, EVEN IF ADVISED OF THE POSSIBILITY OF SUCH DAMAGE.
 */
#ifndef _config_h
#define _config_h

/** \addtogroup config Configuration
 *  Various default settings.
 *  @{
 */

 /** \file config.h
 *  Various default settings.
 */

//  -----------------
// |    Filtering    |
//  -----------------

#define FILTER_KALMAN 0
#define FILTER_COMPLEMENTARY 1
#define ORIENTATION_FILTER FILTER_KALMAN /**< Filter Implementation to be used */

/** Time Contant for Low and High Pass Filter in the Complementary Filter.
 *  In essence, time periods shorter than TAU come from gyro data,
 *  longer time periods come from the Accelerometer data.
 *  In seconds!
 */
#define COMPLEMENTARY_TAU 0.5

// 1 has no effect, bigger numbers dampen the signal more
#define SOFTWARELOWPASS 1 /**< Software Low-Pass on Gyro and ACC */
#define ACCFILTERFACTOR SOFTWARELOWPASS /**< Accelerometer Low Pass Factor */
#define GYROFILTERFACTOR SOFTWARELOWPASS /**< Gyroscope Low Pass Factor */

#define PID_OUTMAX 256 /**< Maximum PID Output */
#define PID_OUTMIN -256 /**< Minimum PID Output */
#define PID_INTMAX PID_OUTMAX /**< Maximum PID Integral Sum */
#define PID_INTMIN PID_OUTMIN /**< Minimal PID Integral Sum */

//  -----------------
// |    Kalman      |
//  -----------------

/** Time Constant */
#define DT 0.01f // 100Hz

// Q (3x3 Matrix) with these elements on diagonal
#define Q1 5.0f /**< Q Matrix Diagonal Element 1 */
#define Q2 100.0f /**< Q Matrix Diagonal Element 2 */
#define Q3 0.01f /**< Q Matrix Diagonal Element 3 */

// R (2x2 Matrix) with these elements on diagonal
#define R1 1000.0f /**< R Matrix Diagonal Element 1 */
#define R2 1000.0f /**< R Matrix Diagonal Element 2 */

//  -----------------
// |       Set       |
//  -----------------

#define SET_ROLLPLUS 1 /**< Second Motor at the Right */
#define SET_ROLLMINUS 3 /**< Fourth Motor at the Left */
#define SET_PITCHPLUS 0 /**< First Motor at the Top */
#define SET_PITCHMINUS 2 /**< Third Motor at the Bottom */

//  -----------------
// |       PID       |
//  -----------------

#define PID_P 5.0 /**< Default PID P Constant */
#define PID_I 0.03 /**< Default PID I Constant */
#define PID_D -13.0 /**< Default PID D Constant */

//  -----------------
// |      Motor      |
//  -----------------

#define MOTORCOUNT 4  /**< Amount of motors */

//  -----------------
// |       ADC       |
//  -----------------

#define BATT_MAX 15 /**< Battery Voltage Reference (ADC 5V) */
#define BATT_CHANNEL 0 /**< ADC Channel for Battery */

//  -----------------
// |       TWI       |
//  -----------------

#define ACC_ADDRESS 0x32 /**< Accelerometer Address (0011001r) */
#define GYRO_ADDRESS 0xD6 /**< Gyroscope Address (110101xr, x = 1) */
#define MAG_ADDRESS 0x3C /**< Magnetometer Address */
#define MOTOR_BASEADDRESS 0x52 /**< Address of first motor controller */

//  -----------------
// |    xyControl    |
//  -----------------

#define LED0PORT PORTL /**< First LED Port */
#define LED0DDR DDRL /**< First LED Data Direction Register */
#define LED0PIN PL6 /**< First LED Pin */
#define LED1PORT PORTL /**< Second LED Port */
#define LED1DDR DDRL /**< Second LED Data Direction Register */
#define LED1PIN PL7 /**< Second LED Pin */
#define LED2PORT PORTG /**< Third LED Port */
#define LED2DDR DDRG /**< Third LED Data Direction Register */
#define LED2PIN PG5 /**< Third LED Pin */
#define LED3PORT PORTE /**< Fourth LED Port */
#define LED3DDR DDRE /**< Fourth LED Data Direction Register */
#define LED3PIN PE2 /**< Fourth LED Pin */

//  -----------------
// |      XMEM       |
//  -----------------
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

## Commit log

2012-11-12 Added bank switching.
    [xyControl.brd, xyControl.sch]
2012-11-15 New 3V3 Regulator.
    [xyControl.brd, xyControl.sch]
2012-11-15 Minor fixes.
    [xyControl.brd]
2012-11-17 Extended XMEM bank switching.
    [xyControl.brd]
2012-11-19 Added config file.
    Also finished first Hardware Revision!
    [xyControl.brd, xyControl.sch]
2012-11-25 Finished SD/MMC Driver.
2012-12-20 Task Manager is properly bank-switching.
2012-12-22 Added Servo Test.
2012-12-30 Started with servo lib.
2013-01-01 Finished servos.c library
2013-01-02 Added TWI and Gyro Libraries.
2013-01-03 Added Accelerometer library.
2013-01-04 Added UART Test.
2013-01-04 Added Accelerometer Test.
2013-01-04 Added Gyroscope Test.
2013-01-05 Java FlightRemote displays Accelerometer data!
2013-01-05 Fixed Gyroscope Code.
2013-01-05 Accelerometer Test calculates pitch and roll.
2013-01-05 Gyro Test calculates X rotation angle.
2013-01-05 Combined Accelerometer and Gyroscope Data.
    Using a simple Complimentary Filter.
2013-01-06 Added Magnetometer Library and Test.
2013-01-12 Added Low level motor library.
    Removed NCurses visualizer. Renamed Java Visualizer. Began with Java
    Telemetry App.
2013-01-12 Fixed Motorlib Test.
2013-01-12 Finished Test Motorlevel
2013-01-14 Added ADC Code.
2013-01-16 Fixed ADC.
2013-01-26 Extended Telemetry Tool. UART Menu Help sorted.
2013-01-26 UART Menu command now unsigned.
2013-01-28 Examples use Task Handler.
    Old examples moved into "old" folder, may will be made task based.
    Library registers stdin, stdout and stderr. More xyLed functionality,
    debug mode for accelerometer driver.
2013-02-11 Ported RAM Test. Fixed standard stream memory location.
    [hardwareTest.c]
2013-02-11 Added Motor Test.
2013-02-14 Removed Motorlevel Test.
    Extended HardwareTest. Fixed stdout, now sending CR.
    [hardwareTest.c]
2013-02-15 Can select UART module at compile time.
2013-02-15 Added Bluetooth Test.
    Can register handler for unhandled UART menu commands.
2013-02-15 Added PID Control.
2013-02-15 Extended UART Flight Firmware.
2013-02-28 Threads in extra files.
2013-03-01 New Button Layout in xyCopter. Can now rotate.
2013-03-02 Increased accelerometer range.
2013-03-02 Normalizing Gyro and ACC in their libraries.
2013-03-03 Multiple changes.
    Combined control library into pid library. All Quadrocopter Controlling
    Libraries no longer have tasks, the task is implemented in UARTFlight.
    The examples folder was removed. UARTFlight is now sending constant
    status updates. Updated xyCopter App to receive and display these
    status updates.
    [config.h, hardwareTest.c]
2013-03-05 Added Connect and Disconnect Buttons.
2013-03-05 Added Software Low-Pass Filter.
2013-03-06 xyCopter displays PID Output
2013-03-06 Now using Kalman Filter.
2013-03-06 Orientation library with error reporting.
    [uartFlight.c]
2013-03-06 Can toggle PID.
2013-03-09 Can change PID Parameters live.
2013-03-13 xyCopter prints voltage in color.
2013-04-14 Can switch between kalman or complementary filter
2013-04-24 Fixed PCB Layout
    SD slot is now rotated correct
    [xyControl.brd]
2013-04-29 Added HardwareTest.
    UART Flight can be silenced. Tries to calculate Yaw angle. Telemetry
    displays Yaw Angle. Mag normalizes output (bug?).
    [Remote.java, config.h, hardwareTest.c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]
2013-05-23 Self-Reset if sensor data is garbage. Some refactoring of function and variable names.
    [uartFlight.c, xycontrol.h]
2013-05-24 PID influence now absolute
2013-05-24 Renamed Global PID Vars. Set Task using 8bit Integer for diff.
2013-05-29 Fixed xyCopter Bug. Bluetooth device selection was broken.
